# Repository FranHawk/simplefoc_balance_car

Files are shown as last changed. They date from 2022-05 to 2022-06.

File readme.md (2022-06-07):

在这里插入图片描述

# 前言
本科毕业于自动化，期间学习了各种电机运动控制原理，自动控制原理，但是只会考试而未究其理。最近接触到simplefoc这个基于arduino的开源无刷电机驱动库，想正好借此机会将本科学到的内容用于实际，于是就有了这个小项目，**基于无刷电机FOC的平衡小车**。
无刷电机相比于普通小车用的有刷电机，相同体积下扭矩更大，无刷电机驱动小车时可以直驱而不像有刷电机需要带减速器才能满足扭矩要求，且响应速度更快。采用无刷电机可以把小车做的更紧凑美观。
无刷电机的驱动电路和算法要更加复杂，无刷电机在低速工作时，算法层面上采用磁场定向控制算法FOC(Field-oriented control),可以精确控制电机的位置，速度乃至电流也就是转矩，由此可以做出很多好玩的东西。基于foc的无刷电机在机器人关节，相机云台电机控制等领域得到广泛应用。
# 主要功能
 - 板载双路无刷电机驱动及电流环芯片，每路最大电流2.5A，可驱动两个云台无刷电机，可控制到电流
 - 小车可自平衡，可通过手机app蓝牙连接控制进退，转向
 - 搭载双排RGB，每排共24个灯，可以扩展成更多，实现多种灯光特效且不影响车辆控制
 - 图传接口，通过外接ESP-CAM模块实现WIFI图传，可在手机上查看(20220421 插口画反用不了。。)
# 开源资料链接
博客文档链接
[https://blog.csdn.net/weixin_42487906/article/details/124898392](https://blog.csdn.net/weixin_42487906/article/details/124898392)

视频链接
[https://www.bilibili.com/video/BV1Sv4y137FG/](https://www.bilibili.com/video/BV1Sv4y137FG/)

github仓库，内有代码，3D打印文件，pcb制板文件：
[https://github.com/FranHawk/simplefoc_balance_car](https://github.com/FranHawk/simplefoc_balance_car)

立创eda工程 可在线查看原理图和pcb：
总共有三个板子
**主板(包括电机控制和驱动部分)**：[https://oshwhub.com/FranHawk/balance_car_esp32_simplefoc](https://oshwhub.com/FranHawk/balance_car_esp32_simplefoc)
**编码器板**：[https://oshwhub.com/FranHawk/as5600-16mm](https://oshwhub.com/FranHawk/as5600-16mm)
**RGB灯带板**：[https://oshwhub.com/FranHawk/rgb_strip](https://oshwhub.com/FranHawk/rgb_strip)
# 材料购买链接
所有的电子元件材料都可以对照BOM表或者工程里的原理图买，在淘宝或者立创上买均可，下面列出一些关键材料的链接

**AS5600 L6234PD INA240A1**：【淘宝】[https://m.tb.cn/h.ft947n2?tk=gn3u2P8IocI](https://m.tb.cn/h.ft947n2?tk=gn3u2P8IocI)「L6234PD L6234D L6234   HSOP 原装汽车IC 进口芯片热卖 质量超好」点击链接直接打开
电机部分的芯片 这个店家买到的货还算便宜
**其他的电子元器件**都可以在优信电子之类的找到，财力充足的可以直接立创，省事。
**2210云台电机（至少两个）**【淘宝】[https://m.tb.cn/h.fslSDE8?tk=G8Pk2P8HluO](https://m.tb.cn/h.fslSDE8?tk=G8Pk2P8HluO)「清仓HJ2210-75T无刷云台电机狗3云台专用 航拍电机 云台空心轴马」点击链接直接打开
**轮胎胎皮（至少两个）** 【淘宝】[https://m.tb.cn/h.ft9UFV4?tk=L8Ez2P8u1Ma](https://m.tb.cn/h.ft9UFV4?tk=L8Ez2P8u1Ma)「AXIAL 1比24车SCX24 90081小米吉姆尼通用橡胶攀爬轮胎皮直径52mm」点击链接直接打开
**电机支架（至少两个）** 【淘宝】[https://m.tb.cn/h.fsl86Kp?tk=i9Oo2P8FvxY](https://m.tb.cn/h.fsl86Kp?tk=i9Oo2P8FvxY)「390电机支架 385固定座 365安装底座 380马达固定架 送螺丝螺母 点击链接直接打开
**黑色亚克力板（至少两个）** 【淘宝】[https://m.tb.cn/h.fH9ybkd?tk=2OCV2P8vqAf](https://m.tb.cn/h.fH9ybkd?tk=2OCV2P8vqAf)「平衡小车DIY专用亚克力支架板扩展板」点击链接直接打开
**电池 900mah**【淘宝】[https://m.tb.cn/h.fGk2f0O?tk=33dF2PjbvTN](https://m.tb.cn/h.fGk2f0O?tk=33dF2PjbvTN)「航模电池5200mAh 11.1V足容高C7.4V车模船模 RC攀爬车质量保证」点击链接直接打开

**其他机械小零件**
 - sh1.0 mm的线，3P和4P的，**注意接线前一定要检查编码器板和主板的线顺序是不是对应的**直接买来的线是不能用的，需要自己焊一下改下顺序
 - m2.5的螺钉，至少8mm长，和m2.5的垫圈若干，用于固定编码器，电机与电机支架
 - m3 6mm长的螺钉，m3*5 6mm的铜柱，m3*20 6mm铜柱，m3螺母若干
 - AB胶或者同等强度的胶，用于将径向磁铁固定在电机轴线处
 - 绑带和魔术贴，用于固定主板和电池
 - 3.81mm插头，用于把电机线插到主板上，XT30公头接口，用于把主板连接电池，红黑电源线

# 制作步骤

## 1.电路部分
打开开源资料链接上的三个pcb工程，在嘉立创投板生产，把元器件都买到并焊上去
**主板**

在这里插入图片描述
在这里插入图片描述
按照上图用红黑电源线焊接主板和XT30 公头插头

**编码器板**
在这里插入图片描述
编码器板没什么元器件，记得上面这个焊点要焊上，背面还有一个as5600芯片，总共要做两个
**RGB灯板**
在这里插入图片描述
把灯焊上去，没什么好说的，总共要做两个

**sh1.0 3P和4P的线**
分别做两条，用作连接RGB板和编码器板到主板，注意接线前一定要检查编码器板和主板的线顺序是不是对应的，我买到的反的，需要自己调换顺序

## 机械部分
制作两个电机部分
在这里插入图片描述
先把径向磁铁粘在电机轴心
在这里插入图片描述
把编码器板，电机支架和电机用m2.5螺钉按上图组装，中间加些垫片，防止相互间摩擦，如下图
在这里插入图片描述
3D打印轮毂，套在电机上，再套上胎皮，3D打印文件在github里
在这里插入图片描述
## 组装
3D打印固定板，用魔术贴和扎带固定电池，用m3*5 铜柱和螺钉将3D打印固定板和主板组装
在这里插入图片描述
在这里插入图片描述
将两个电机部分和主板部分用m3螺钉组装，电机线通过3.8mm 插头连接到主板，顺序随意。编码器板用sh1.0 mm 4P线连接，第一层亚克力板上装四个m3 20mm的铜柱，如下图
在这里插入图片描述
RGB灯板和第二层亚克力板粘在一起
在这里插入图片描述
连接RGB的线到主板，固定第一层和第二层亚克力板，完成组装
在这里插入图片描述
## 烧写程序
通过vscode+platformio来烧写程序
第一次烧写程序前，先找到hw_bldc.cpp里的hw_bldc_init()函数里
有这样几句

```c
    motor_0.init();
    motor_1.init();
    
    motor_0.initFOC();
    motor_1.initFOC();
```
第一次烧写时，initFOC里不需要有参数，上电后simplefoc会运行自检程序，检测电机旋转方向和电角度，会在串口中输出，通过串口得到参数后填入initFOC

```c
	motor_0.init();
    motor_1.init();
    
    motor_0.initFOC(4.53, Direction::CW);
    motor_1.initFOC(0.64, Direction::CCW);
```
如上，每个人的这两个参数都是不一样的，然后第二次烧写代码。之后每次启动就不会消耗时间自检了。

## 手机控制
手机安装点灯APP，[https://diandeng.tech/dev](https://diandeng.tech/dev)
创建一个蓝牙设备，添加一个手柄控件，起名叫JoyKey
在这里插入图片描述
在这里插入图片描述
对于灯光效果的遥控可自行开发

# 硬件分析与概要设计
电路部分分为一个主板，两个编码器小板，两个RGB灯板
- 其中主板部分集成了无刷电机驱动，控制部分，MPU6050传感器，供电，串口和各种接口
- 驱动器板搭载AS5600磁编码器，通过IIC与主板通信
- 主板为RGB提供5V电源与控制信号
电机采用2210无刷云台电机，7对极
## 无刷电机驱动部分
驱动是小车的核心部分，是小车动起来的关键。无刷电机转动时需要分别控制电机的三相电压。采用FOC算法控制时，还需要位置传感器提供转子和定子的相对位置，如果要控制转矩，还需要电流传感器。初次学习FOC，我采用灯哥开源FOC驱动的方案，[灯哥github仓库地址](https://github.com/ToanTech/Deng-s-foc-controller)。
电机驱动采用L6234P三相H桥集成驱动芯片
在这里插入图片描述
电流检测采用INA240A2芯片，放大增益为50，这个芯片也比较贵，可以用INA240A1代替，放大增益为20，我焊的时候用的就是这个，一样能用。
在这里插入图片描述
电机位置检测采用AS5600绝对值磁编码器芯片，IIC通讯，我为这个芯片画了个小板子附在电机轴处，与主板相连，同时还需要在电机轴线处固定一个径向磁铁。
在这里插入图片描述
在这里插入图片描述

## 控制部分
由主要功能可知，需要MCU具有蓝牙和WIFI功能，还需要足够的性能用于FOC算法，同时控制RGB。最近看到的esp32可以说正合适，esp32有320K RAM，4M ROM，两个core，一个核专门用来跑foc算法，另外一个核用来跑其他程序包括RGB控制，simplefoc官网上说esp32单次foc运算能有1ms，引脚也足够多，满足平衡控制的需求。
在这里插入图片描述
## 传感部分
平衡控制需要通过传感器检测到小车自身的姿态，我采用最常见的MPU6050 6轴加速度计陀螺仪芯片
在这里插入图片描述
WIFI图传由主板通过2.54排母插接ESP-CAM模块实现
在这里插入图片描述
## 电源部分
- 电池选用3S 900mah航模电池，提供12V电压给电机
- TPS5430开关芯片将12V转5V，供给到RGB和ESP-CAM模块
- AMS1117将5V降到3.3V
 在这里插入图片描述
 在这里插入图片描述
## RGB部分
RGB采用WS1802B LED灯，MCU一个IO口就可以驱动一串RGB
在这里插入图片描述
在这里插入图片描述

## 其他
其他一些接口和转串口芯片什么就不多介绍了，可以看我开源的电路工程了解

# 理论基础
无刷电机平衡小车的理论部分需要了解

1.无刷电机磁场定向控制FOC算法
2.平衡车建模和控制算法

理论部分网上有很多资料，讲解也非常清楚易懂，珠玉在前，我引出一些比较好的文章，供想要深究的读者查看
## 磁场定向控制FOC算法
FOC算法的内容比较多，初学者可以看下稚晖君这篇文章，比较通俗易懂
- [深入浅出讲解FOC算法与SVPWM技术](https://zhuanlan.zhihu.com/p/147659820)

simplefoc官方文档的介绍也比较详细，还有源码讲解，代码中也用到了simplefoc的库，所以最好去官网文档了解一些simplefoc的使用方法
[https://simplefoc.com/](https://simplefoc.com/)

其他比较好的文章
 - [BLDC电机控制算法——FOC简述](https://blog.csdn.net/qq_26285867/article/details/82079450)
 - [foc学习笔记1——准备工作](https://blog.csdn.net/jdhfusk/article/details/120395938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)
 ## 平衡车建模和控制算法
 - 平衡车建模部分首推 清华卓晴的平衡车参考方案 对平衡车的数学模型的建立有非常清晰的介绍，需要熟悉平衡车模型的可以多看几遍
- 平衡车平衡环和速度环pid的整定可以看这篇文章
 [平衡小车PID，就该这么调！！！](https://blog.csdn.net/best_xiaolong/article/details/105153978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)

# 软件部分
ESP32这款MCU有两个核心，我采用freertos来对两个核进行调度，整体软件框架基于arduino+freertos

## 用到的库
[Adafruit_NeoPixel](https://github.com/adafruit/Adafruit_NeoPixel) 用于驱动RGB灯带
[blinker-library](https://github.com/blinker-iot/blinker-library)点灯科技的蓝牙库，可以通过手机app和平衡车蓝牙通讯
[MPU6050_light](https://github.com/rfetick/MPU6050_light)MPU6050驱动库
[Arduino-FOC](https://github.com/simplefoc/Arduino-FOC)simplefoc的arduino支持库

**0 core：**
task 0：simplefoc的电流环的运算、俯仰角数据读取的和电机电压的输出
**1 core：**
task 1：平衡环和速度环pid运算
task 2：RGB闪烁和通过蓝牙接收手机的控制命令

## TASK 0
这个任务的代码比较简单，loopFOC和move负责simplefoc电流环的运算和电压输出
mpu.update()读出MPU6050数据并返回俯仰角，俯仰角通过互补滤波结算得到就可以了
shaftVelocity返回电机速度，用于task 1速度环pid的运算

```c
void task_motor_move(void *pvParameters)
{
    while (1)
    {
        // iterative setting FOC phase voltage
        motor_1.loopFOC();
        motor_0.loopFOC();
        // Serial.printf("d:%f,%f\n",motor_1.shaftVelocity(),motor_0.shaftVelocity());
        motor_1.move(motor_output_left);
        motor_0.move(motor_output_right);

        // // iterative function setting the outter loop target
        mpu.update();

        speed_right = motor_0.shaftVelocity();
        speed_left = motor_1.shaftVelocity();
    }
}
```
## TASK 1
该任务主要是平衡环和速度环pid运算，用状态机的思维将平衡车状态分为STOP，RUNNING，PICKUP三个状态，这样做主要是为了避免平衡车被拿起时电机疯转。
开机时状态为STOP，把车扶正到平衡位置附近则进入RUNNING状态，当拿起倾斜角后过大，则进入PICKUP状态，逆时针旋转车体后进入STOP状态。
RUNNING状态运行平衡环，速度环和角度环。平衡环采用pd，速度环用pi，角度环仅用单p。

```c
void task_control(void *pvParameters)
{
    while (1)
    {
        angle_pitch = mpu.getAngleY();
        // Serial.printf("d:%f\n",angle_pitch);
        acc_Z = mpu.getAccZ();
        if (running_state == STATE_STOP)
        {
            if (abs(angle_pitch - angle_pitch_offset) < 0.5)
            {
                running_state = STATE_RUNNING;
            }
        }
        else if (running_state == STATE_RUNNING)
        {
            speed_average = (speed_right + speed_left) / 2;
            if (abs(angle_pitch - angle_pitch_offset) > 50 )
            {
                speed_I_sum=0;//清空积分系数
                running_state = STATE_PICKUP;
            }
            else
            {
                speed_target = translate_speed;

                speed_error = speed_target - speed_average;

                speed_I_sum+=(speed_error*speed_I);
                if(speed_I_sum>15){
                    speed_I_sum = 15;
                }
                if(speed_I_sum<-15){ 
                    speed_I_sum = -15;
                }
                angle_target_pitch = speed_P * speed_error + speed_I_sum;
  
                motor_output_left = angle_P * ((angle_pitch - angle_pitch_offset) - angle_target_pitch) + angle_D * mpu.getGyroY()+rotate_speed; //+ angle_D * mpu.getGyroY()
                motor_output_right = angle_P * ((angle_pitch - angle_pitch_offset) - angle_target_pitch) + angle_D * mpu.getGyroY()-rotate_speed;
                angle_last_pitch = angle_pitch;
            }
        }
        else if (running_state == STATE_PICKUP)
        {
            motor_output_left = 0;
            motor_output_right = 0;
            if (speed_right > 3.14 && speed_left < -3.14)
            {
                running_state = STATE_STOP;
            }
        }
        vTaskDelay(1);
    }
}
```

## TASK 2
task 2用于RGB效果显示，和接收手机blinker app通过蓝牙发送的数据。一般的RGB等效都有一个延时函数，普通的延时函数都是在原地死等，这样大大降低CPU效率，影响其他程序运行，这里我编写了一系列非阻塞式RGB灯效：在显示完灯效后不再原地延时，而是直接进行调度，切换到其他task。详细可看我代码。

```c
void task_neopixel(void *pvParameters)
{
    uint32_t neopixel_pattern_previous = 0;
    uint32_t neopixel_pattern_interval = 500;
    uint32_t neopixel_pattern_number = 0;
    while (1)
    {
        // 效果切换
        if((neopixel_count-neopixel_pattern_previous)>neopixel_pattern_interval){
            neopixel_pattern_previous = neopixel_count;
            neopixel_pattern_number++;
            neopixel_state_clear(strip_1_handler);
            neopixel_state_clear(strip_2_handler);
            if(neopixel_pattern_number>4){
                neopixel_pattern_number = 0;
            }
        }

        switch(neopixel_pattern_number){
            case 0:
                neopixel_police_style_2(strip_2_handler,10,5);
                neopixel_police_style_2(strip_1_handler,10,5);
                break;
            case 1:
                neopixel_police_style_1(strip_2_handler,10,5);
                neopixel_police_style_1(strip_1_handler,10,5);
                break;
            case 2:
                neopixel_loop(strip_2_handler, 255, 255, 255, 4, 4);
                neopixel_rainbow(strip_1_handler);
                break;
            case 3:
                neopixel_bounce(strip_1_handler, 0, 255, 0, 2, 3, 0);
                neopixel_fade_in_out(strip_2_handler, 255, 0, 255, 2, 1,25);
                break;
            case 4:
                neopixel_spread_out(strip_2_handler, strip_2_handler.strip.Color(0,255,0), strip_2_handler.strip.Color(0,0,255), 4, 10);
                neopixel_spread_out(strip_1_handler, strip_1_handler.strip.Color(255,0,0), strip_1_handler.strip.Color(255,255,0), 4, 10);
                break;
            default:
                break;
        }
        neopixel_count++;

#ifdef USE_BLINKER
        Blinker.run();
#endif

        vTaskDelay(10);
    }
}
```

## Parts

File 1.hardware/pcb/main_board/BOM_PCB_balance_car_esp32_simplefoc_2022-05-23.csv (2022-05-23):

ID | Name | Designator | Footprint | Quantity | Manufacturer Part | Manufacturer | Supplier | Supplier Part | Price
1 | 4.7k | R8,R9,R10,R12,R13,R14 | R0603 | 6
2 | 0.1u | C29,C1,C7,C8,C10,C11,C13,C15,C17,C31,C32,C33,C34 | C0603 | 13
3 | 0.01u | C28,C3,C6,C9,C14 | C0603 | 5
4 | 4.7u | C4,C5 | C0603 | 2
5 | 100nF | C18,C19 | C0805 | 2 | C0805X104K101T | HEC(Holy Stone Enterprise) | LCSC | C485772 | 0.1212
6 | 100uF | C20,C24,C30,C2 | CAP-SMD_BD6.3-L6.6-W6.6-FD | 4 | RVE1V101M0607 | ROQANG | LCSC | C99837 | 0.3251
7 | 220nF | C21,C22 | C0805 | 2 | CL21B224KBFNNNE | SAMSUNG | LCSC | C5378 | 0.083
8 | 10nF | C23,C25 | C0805 | 2 | CL21A106KAYNNNE | SAMSUNG | LCSC | C15850 | 0.0833
9 | 1uF | C26,C27 | C0805 | 2 | CL21B105KBFNNNE | SAMSUNG | LCSC | C28323 | 0.055
10 | HDGC1002WR-S-4P | CN2,CN3 | CONN-SMD_4P-P1.00_HDGC_HDGC1002WR-S-4P | 2 | HDGC1002WR-S-4P | HDGC(华德共创) | LCSC | C2936214 | 0.4043
11 | HDGC1002WR-S-3P | CN4,CN5 | CONN-SMD_3P-P1.00_HDGC_HDGC1002WR-S-3P | 2 | HDGC1002WR-S-3P | HDGC(华德共创) | LCSC | C2936213 | 0.3172
12 | KH-15EDGRC-3.81-3PG | CN6,CN7 | CONN-TH_KH-15EDGRC-3.81-3PG | 2 | KH-15EDGRC-3.81-3PG | kinghelm(金航标) | LCSC | C2761212 | 0.595
13 | SS54_C727065 | D2 | SMA_L4.3-W2.6-LS5.0-RD | 1 | SS54 | TWGMC | LCSC | C727065 | 0.3798
14 | LBAT54SLT1G | D3,D1 | SOT-23_L2.9-W1.3-P1.90-LS2.4-BR | 2 | LBAT54SLT1G | LRC | LCSC | C12765 | 0.1186
15 | 22uH | L1 | IND-SMD_L7.1-W6.6 | 1 | MWSA0603-220MT | Sunlord | LCSC | C132137 | 1.7194
16 | LED-0603_G | LED3V3 | LED0603_GREEN | 1 | 19-217/GHC-YR1S2/3T | EVERLIGHT(台湾亿光) | LCSC | C72043 | 0.1766
17 | 安装孔 | M1,M2,M3,M4 | M3安装孔 | 4 |  |  | yacter
18 | S8050_C908252 | Q1,Q3 | SOT-23-3_L2.9-W1.3-P1.90-LS2.4-BR | 2 | S8050 | FUXINSEMI | LCSC | C908252 | 0.0778
19 | 10k | R1,R3,R4,R17,R18 | R0603 | 5
20 | 3.3k | R2 | R0603 | 1
21 | 0.01 | R5,R6,R15,R16 | R1206 | 4 | RTT06R010FTP | RALEC | LCSC | C104920 | 0.1223
22 | 0 | R7 | R0603 | 1
23 | 3k | R11 | R0603 | 1
24 | ESP32-WROOM-32D | U1 | WIFIM-SMD_39P-L25.5-W18.0-P1.27-BL | 1 | ESP32-WROOM-32D | ESPRESSIF 乐鑫 | LCSC | C473012 | 22.87
25 | L6234PD013TR | U2,U5 | POWERSO20_L15.9-W11.0-P1.27-LS14.2-BL-EP | 2 | L6234PD013TR | STMicroelectronics | LCSC | C77581 | 34.19
26 | CH340C | U3 | SOP-16_L10.0-W3.9-P1.27-LS6.0-BL | 1 | CH340C | WCH | LCSC | C84681 | 2.7
27 | MPU-6050_C24112 | U4 | QFN-24_L4.0-W4.0-P0.50-BL-MPU-6050 | 1 | MPU-6050 | InvenSense | LCSC | C24112 | 66.82
28 | AMS1117-3.3_C347222 | U6 | SOT-223_L6.7-W3.5-P2.30-BR | 1 | AMS1117-3.3 | Youtai Semiconductor Co., Ltd. | LCSC | C347222 | 0.3787
29 | INA240A2PWR | U7,U9,U10,U11 | TSSOP-8_L4.4-W3.0-P0.65-LS6.4-BL | 4 | INA240A2PWR | TI | LCSC | C129949 | 62.13
30 | TPS5430DDAR | U8 | SOIC-8_L5.0-W4.0-P1.27-LS6.0-BL-EP | 1 | TPS5430DDAR | TI | LCSC | C9864 | 5.03
31 | TYPE-C-31-M-31 | USB1 | USB-C-SMD_TYPE-C-31-M-31 | 1 | TYPE-C-31-M-31 | 韩国韩荣 | LCSC | C2760486 | 1.3711
32 | Changzhou | CN8 | CONN-TH_XT30UPB-F | 1 | XT30UPB-F | Changzhou Amass Elec | LCSC | C108769 | 2.76
33 | ESP32-CAM-Ai-Thinker | CN1 | ESP32-CAM | 1 | ESP32-CAM
34 | 2.2nf | C12 | C0603 | 1
35 | 10u | C16 | C0603 | 1 | C344022
36 | TS-1101S-B-B-B-W-A | KEY1 | SW-SMD_L6.0-W3.5-LS8.0 | 1 | TS-1101S-B-B-B-W-A | XKB Connectivity | LCSC | C692465 | 0.2776
37 | KF1027B-01P-G00-ON-01B | SW2 | SW-SMD_2P-L3.5-W6.2-P2.54-LS9.8 | 1 | KF1027B-01P-G00-ON-01B | 凯峰 | LCSC | C976363 | 2.08

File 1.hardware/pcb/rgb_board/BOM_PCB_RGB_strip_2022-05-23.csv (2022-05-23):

ID | Name | Designator | Footprint | Quantity | Manufacturer Part | Manufacturer | Supplier | Supplier Part | Price
1 | WS2812B-MINI | LED1,LED2,LED3,LED4,LED5,LED6,LED7,LED8,LED9,LED10,LED11,LED12,LED13,LED14,LED15,LED16,LED17,LED18,LED19,LED20,LED21,LED22,LED23,LED24 | LED-SMD_4P-L3.5-W3.5-TL_WS2812B | 24 | WS2812B-Mini | Worldsemi | LCSC | C527089 | 0.7028
2 | Pad | P1,P2,P3 | 测试点2MM | 3
3 | HDGC1002WR-S-3P | CN5 | CONN-SMD_3P-P1.00_HDGC_HDGC1002WR-S-3P | 1 | HDGC1002WR-S-3P | HDGC(华德共创) | LCSC | C2936213 | 0.3172

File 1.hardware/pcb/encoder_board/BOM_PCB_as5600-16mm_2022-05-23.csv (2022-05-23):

ID | Name | Designator | Footprint | Quantity | Manufacturer Part | Manufacturer | Supplier | Supplier Part | Price
1 | 100nf | C1 | C0603 | 1
2 | 10u | C2 | C0603 | 1
3 | HDGC1002WR-S-4P | CN1 | CONN-SMD_4P-P1.00_HDGC_HDGC1002WR-S-4P | 1 | HDGC1002WR-S-4P | HDGC(华德共创) | LCSC | C2936214 | 0.4043
4 | HDGC1002WR-S-3P | CN2 | CONN-SMD_3P-P1.00_HDGC_HDGC1002WR-S-3P | 1 | HDGC1002WR-S-3P | HDGC(华德共创) | LCSC | C2936213 | 0.3172
5 | HDR-F-2.54_1x3 | H1 | HDR-F-2.54_1X3 | 1 |  |  | LCSC | C146690 | 0.5625
6 | HDR-M-2.54_1x4 | J1 | HDR-M-2.54_1X4 | 1 |  |  | LCSC | C124378 | 0.2972
7 | 短路连接点 | NO1,NO2,NO3 | 短路连接点 | 3 |  |  | MONIK2020
8 | 4.7k | R1,R2 | R0603 | 2
9 | 10K | R3 | R0603 | 1
10 | AS5600-ASOM | U1 | SOIC-8_L5.0-W4.0-P1.27-LS6.0-BL | 1 | AS5600-ASOM | Ams | LCSC | C79815 | 17.66

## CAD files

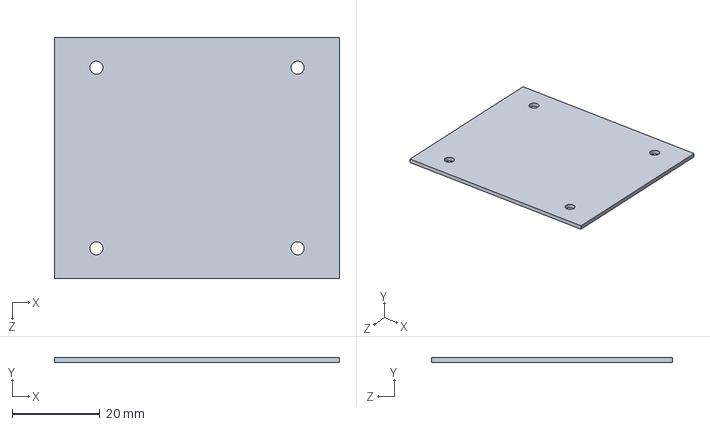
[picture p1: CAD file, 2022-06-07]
1.hardware/stl/pcb固定板.SLDPRT
65.0 x 1.20 x 55.0 mm

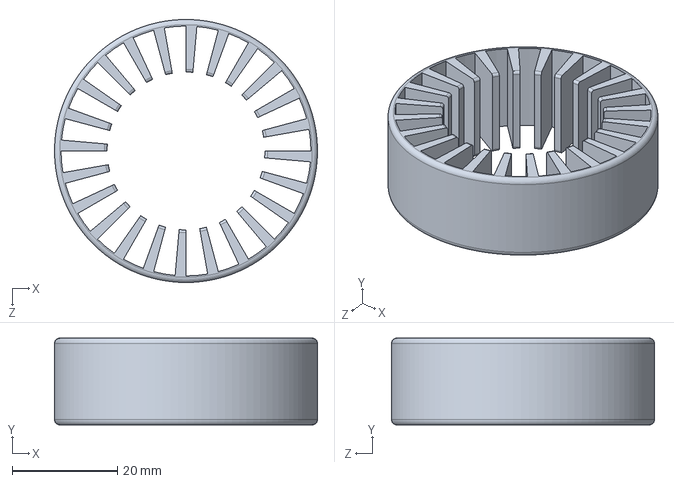
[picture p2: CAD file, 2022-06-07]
1.hardware/stl/轮毂.SLDPRT
50.0 x 16.5 x 50.0 mm

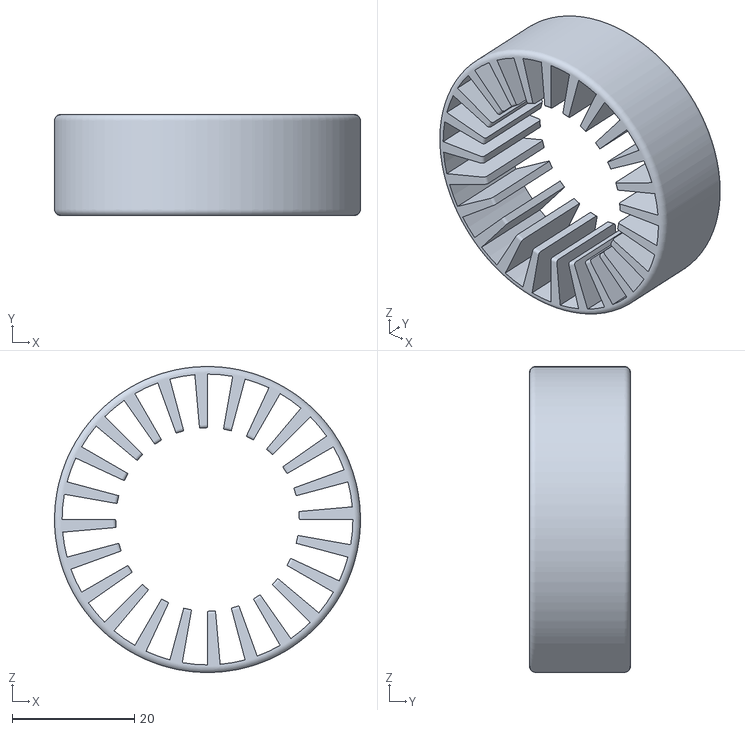
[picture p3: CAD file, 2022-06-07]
1.hardware/stl/wheel.STL
50.0 x 16.5 x 50.0

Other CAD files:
1.hardware/stl/pcb固定板.STL

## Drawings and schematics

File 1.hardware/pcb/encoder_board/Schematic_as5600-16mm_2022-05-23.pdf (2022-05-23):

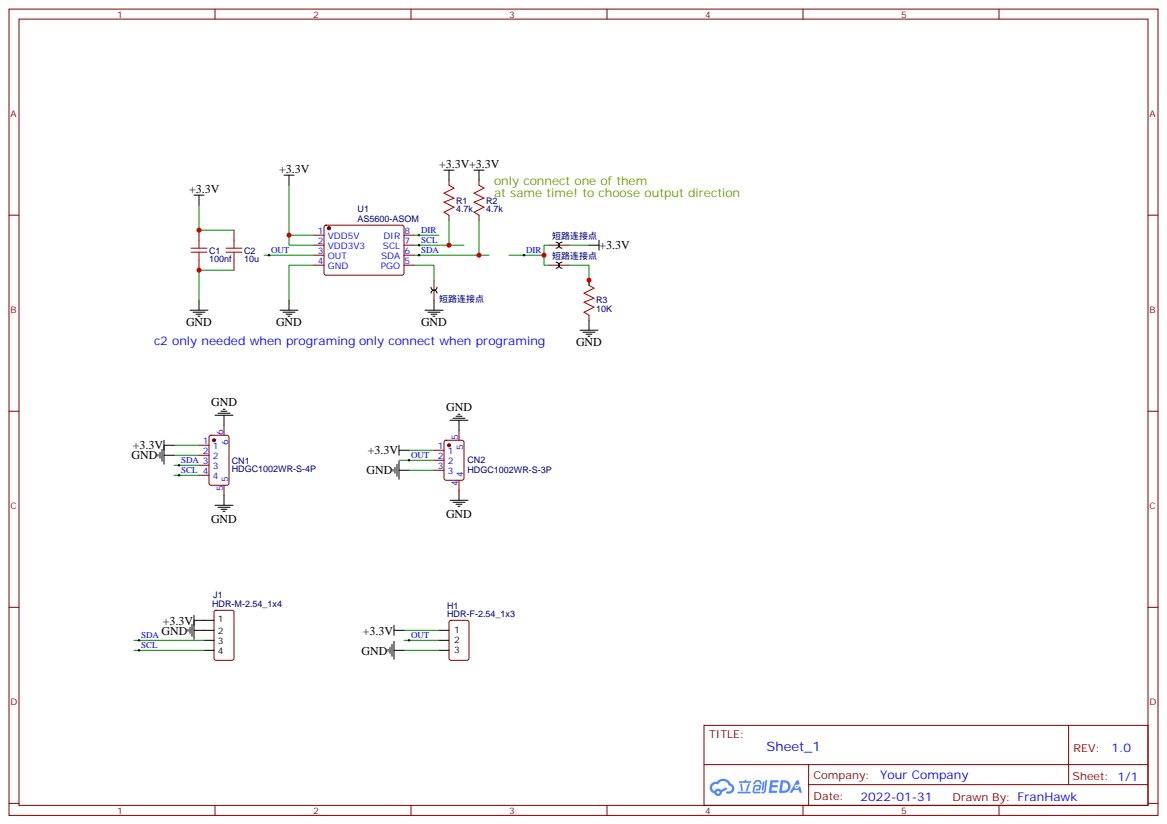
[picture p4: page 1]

only connect one of them
at same time! to choose output direction

GND
c2 only needed when programing only connect when programing

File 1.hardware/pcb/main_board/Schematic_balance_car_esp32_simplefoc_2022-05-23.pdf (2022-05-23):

12V->5V

# MPU6050

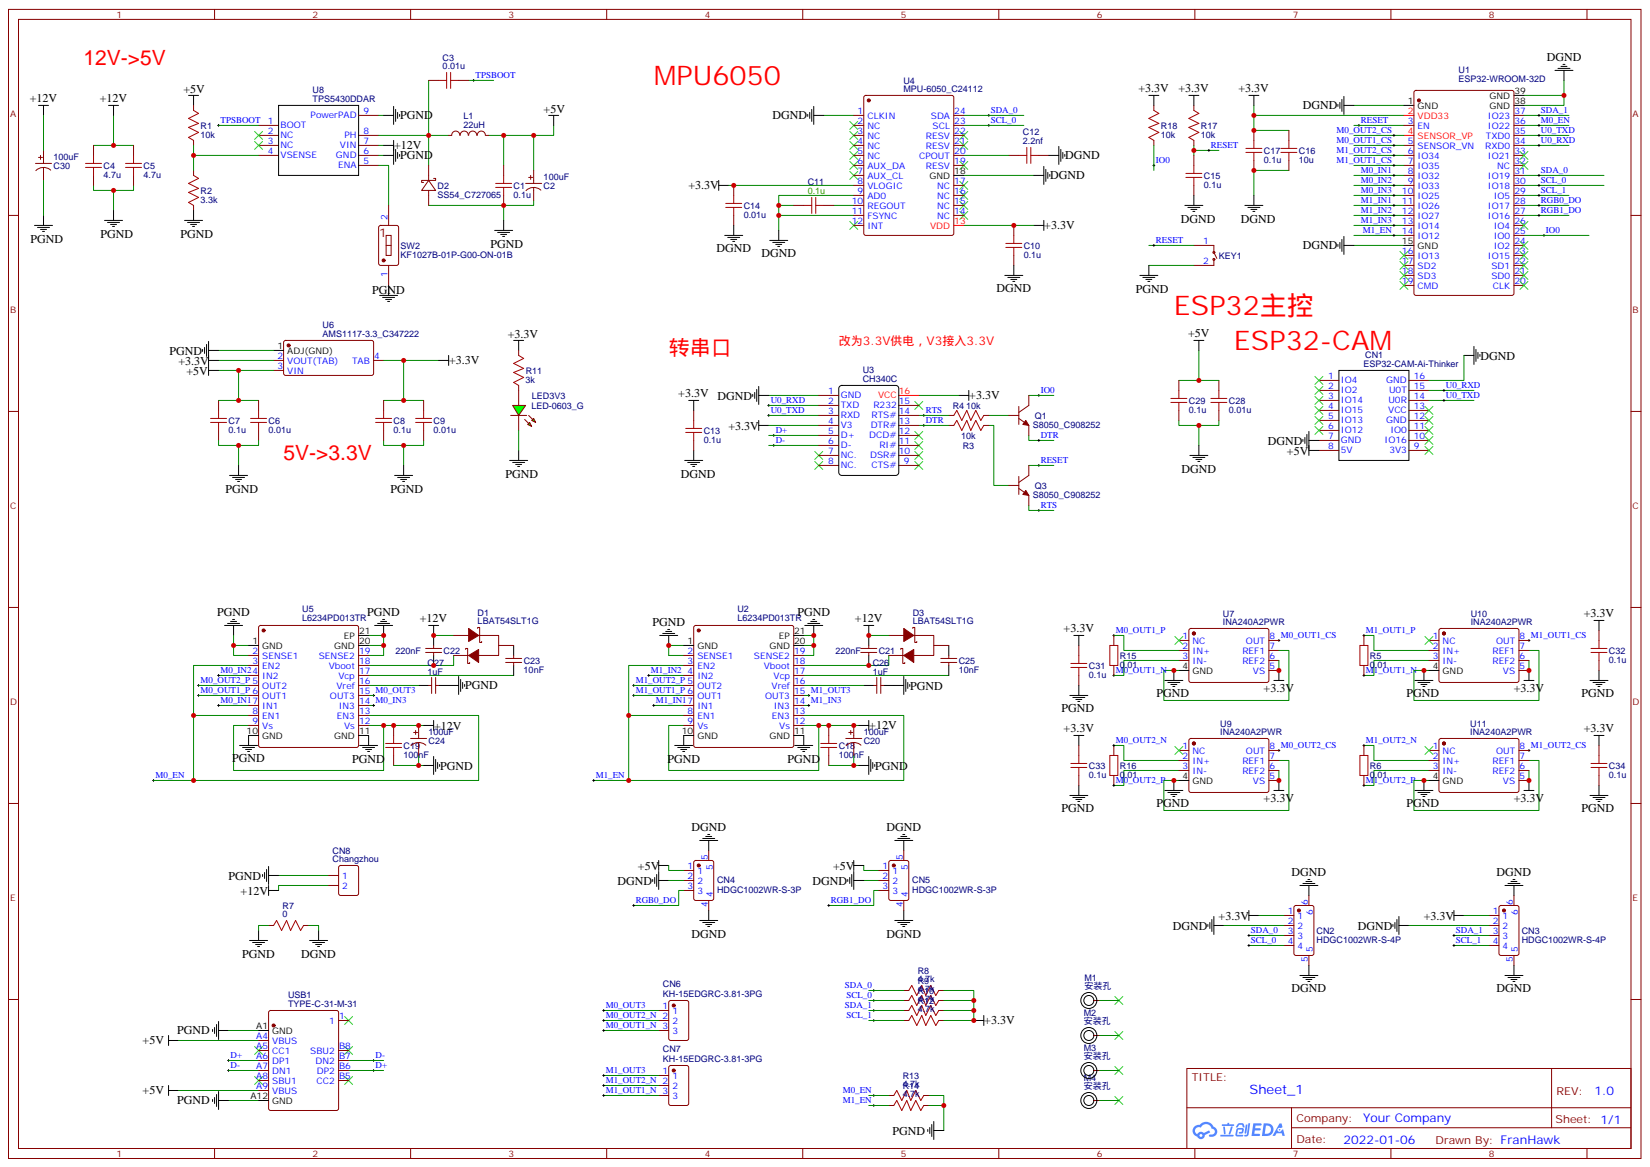
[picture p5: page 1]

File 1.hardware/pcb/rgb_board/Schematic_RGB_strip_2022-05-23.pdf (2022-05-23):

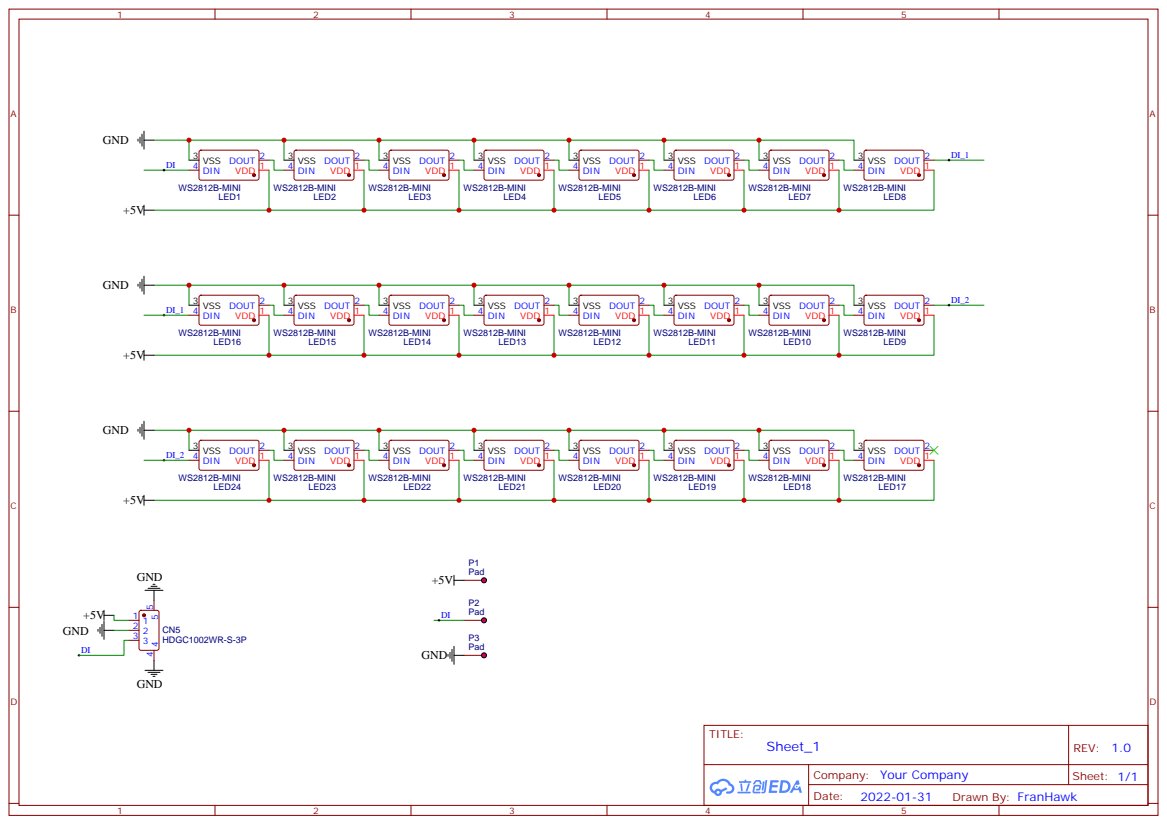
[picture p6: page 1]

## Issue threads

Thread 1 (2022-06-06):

老哥做完了吗？

South-River, 2022-06-06:
做的咋样，发个视频？我等过两周考完试也开干，零件都到齐了2333

FranHawk, 2022-06-07:
做完了，发到b站上了

South-River, 2022-06-07:
不会你是看了我寒假发的半成品视频吧😂。厉害，👍

FranHawk, 2022-06-07:
我也是寒假开始做的，可以给个视频链接吗，我还没看过你做的

South-River, 2022-06-07:
2333我上周删了，没事没事

South-River, 2022-06-07:
哈哈想起来又去翻了翻相册，确实很巧2333，都用的rc轮胎，外形设计也挺像∠( ᐛ 」∠)_
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

Closed 2022-06-09.

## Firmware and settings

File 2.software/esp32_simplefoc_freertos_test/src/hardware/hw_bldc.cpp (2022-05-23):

#include "hw_bldc.h"

// BLDC motor & driver instance
BLDCMotor motor_0 = BLDCMotor(PP_NUMBER);
BLDCDriver3PWM driver_0 = BLDCDriver3PWM(M0_OUTPUT_1, M0_OUTPUT_2, M0_OUTPUT_3, M0_OUTPUT_ENABLE);

BLDCMotor motor_1 = BLDCMotor(PP_NUMBER);
BLDCDriver3PWM driver_1 = BLDCDriver3PWM(M1_OUTPUT_1, M1_OUTPUT_2, M1_OUTPUT_3, M1_OUTPUT_ENABLE);

// encoder instance
MagneticSensorI2C sensor_0 = MagneticSensorI2C(AS5600_I2C);
TwoWire I2C_0 = TwoWire(1);

MagneticSensorI2C sensor_1 = MagneticSensorI2C(AS5600_I2C);
TwoWire I2C_1 = TwoWire(0);

// inline current sensor instance
// check if your board has R010 (0.01 ohm resistor) or R006 (0.006 mOhm resistor)
// InlineCurrentSense current_sense_0 = InlineCurrentSense(0.01, 20.0, M0_CURRENT_IN_1, M0_CURRENT_IN_2);

// InlineCurrentSense current_sense_1 = InlineCurrentSense(0.01, 20.0, M1_CURRENT_IN_1, M1_CURRENT_IN_2);

void hw_bldc_motor_init()
{
    motor_0.useMonitoring(Serial);
    motor_1.useMonitoring(Serial);

    I2C_0.begin(M0_I2C_SDA, M0_I2C_SCL, 400000);
    sensor_0.init(&I2C_0);
    motor_0.linkSensor(&sensor_0);
    I2C_1.begin(M1_I2C_SDA, M1_I2C_SCL, 400000);
    sensor_1.init(&I2C_1);
    motor_1.linkSensor(&sensor_1);

    // driver config
    // power supply voltage [V]
    driver_0.voltage_power_supply = 12.0;
    driver_0.init();
    driver_1.voltage_power_supply = 12.0;
    driver_1.init();
    
    // link driver
    motor_0.linkDriver(&driver_0);
    motor_1.linkDriver(&driver_1);

    // 电流限制
    motor_0.current_limit = 2;
    motor_1.current_limit = 2;

    // 电压限制
    motor_0.voltage_limit = 12;
    motor_1.voltage_limit = 12;

    motor_0.phase_resistance = 12.4; // 12.5 Ohms
    motor_0.torque_controller = TorqueControlType::voltage;
    motor_1.phase_resistance = 14.0; // 12.5 Ohms
    motor_1.torque_controller = TorqueControlType::voltage;

    // // TorqueControlType::foc_current
    // // 其他模式 TorqueControlType::voltage TorqueControlType::dc_current
    // motor_0.torque_controller = TorqueControlType::foc_current;
    // motor_1.torque_controller = TorqueControlType::foc_current;
    // motor_0.torque_controller = TorqueControlType::dc_current;
    // motor_1.torque_controller = TorqueControlType::dc_current;
    
    // set control loop type to be used
    motor_0.controller = MotionControlType::torque;
    motor_1.controller = MotionControlType::torque;

    // contoller configuration based on the controll type
    // motor_0.PID_current_q.P = 5;
    // motor_0.PID_current_q.I = 1000;
    // motor_0.LPF_current_q.Tf = 0.01;
    // motor_1.PID_current_q.P = 5;
    // motor_1.PID_current_q.I = 1000;
    // motor_1.LPF_current_q.Tf = 0.01;

    // velocity low pass filtering time constant
    motor_0.LPF_velocity.Tf = 0.01;
    motor_1.LPF_velocity.Tf = 0.01;

    // current sense init and linking
    // current_sense_0.init();
    // current_sense_0.gain_b *= -1;
    // //current_sense_0.skip_align = true;
    // motor_0.linkCurrentSense(&current_sense_0);
    // current_sense_1.init();
    // current_sense_1.gain_b *= -1;
    // //current_sense_1.skip_align = true;
    // motor_1.linkCurrentSense(&current_sense_1);

    // initialise motor

    
    motor_0.init();
    motor_1.init();
    
    // align encoder and start FOC
    // motor.initFOC(2.15, Direction::CW);
    motor_0.initFOC(4.53, Direction::CW);
    motor_1.initFOC(3.33, Direction::CCW);

    motor_0.motion_downsample=0;
    motor_1.motion_downsample=0;

    // set the inital target value
    motor_0.target = 0.3;
    motor_1.target = 0.3;
}

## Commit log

2022-06-07 second push
    [pcb固定板.SLDPRT, pcb固定板.STL, wheel.STL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]
2022-06-28 修改platformio.ini
